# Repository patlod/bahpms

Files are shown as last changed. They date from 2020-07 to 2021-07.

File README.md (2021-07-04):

# bahpms

Thesis Project:  Development and Evaluation of a Hybrid Power Management System for Airships Intended for Infrared Thermographic Inspection of Photovoltaic Plants

## Airship Prototype
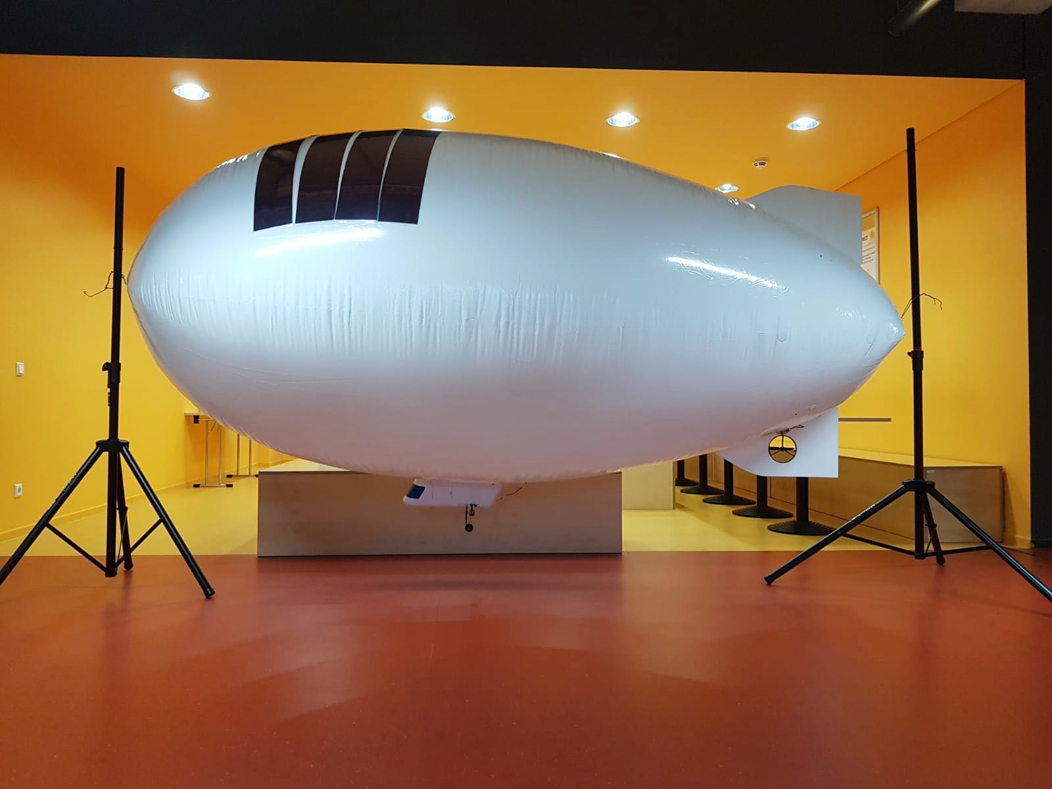
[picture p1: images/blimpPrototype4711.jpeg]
Airship


## Concept
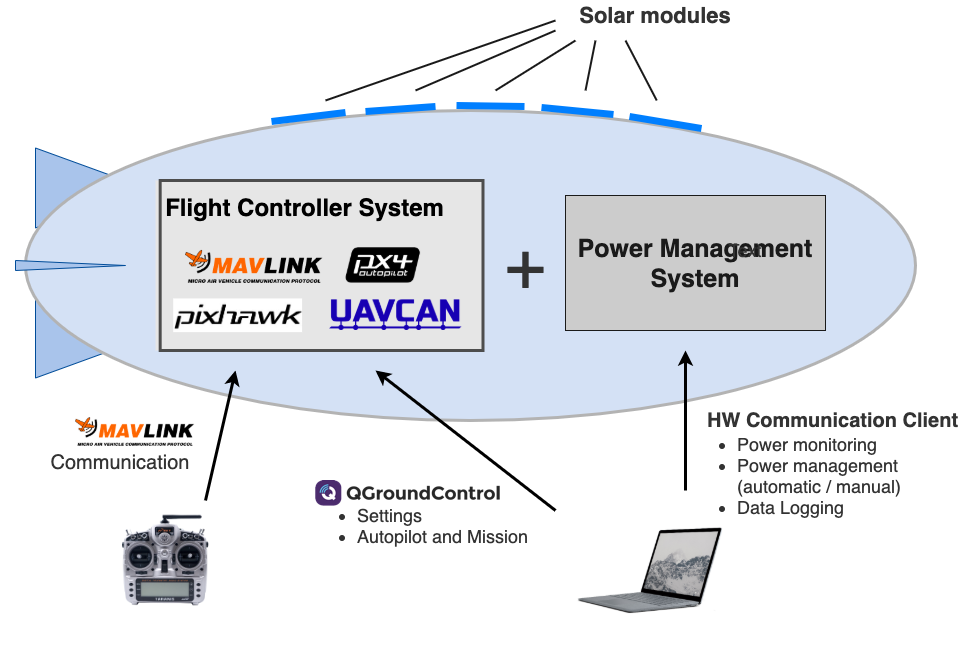
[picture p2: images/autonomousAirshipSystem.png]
Autonomous Airship System


### Inteded Mission
While vehcile monitors photovoltaic plants it will extend its flight time by charging itself with solar power.

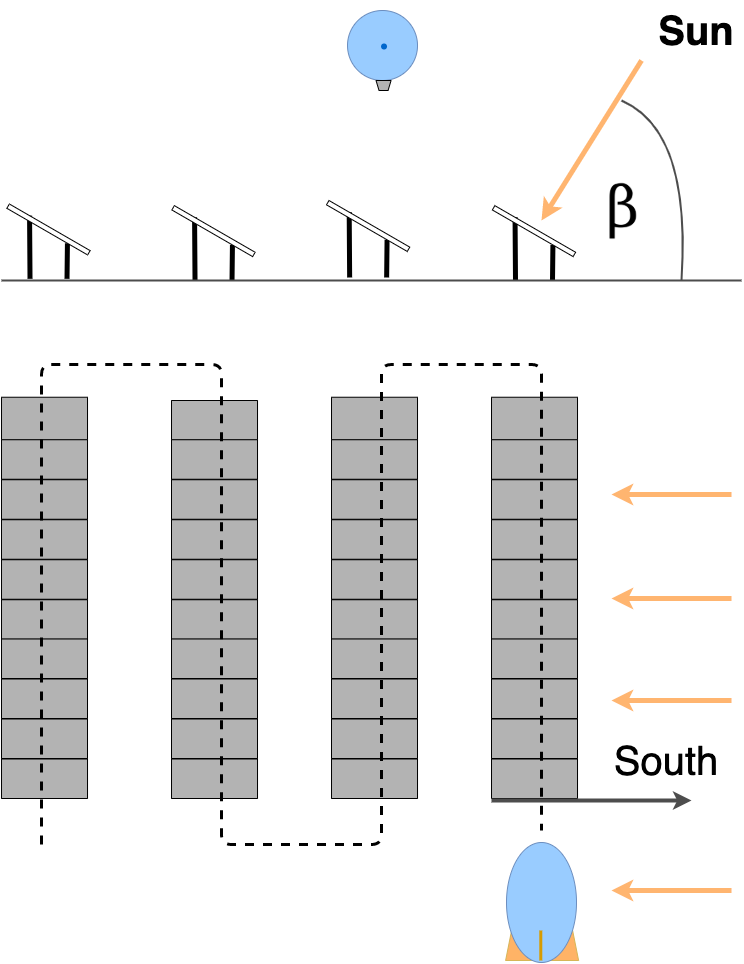
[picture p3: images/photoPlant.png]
PV Plant Monitoring

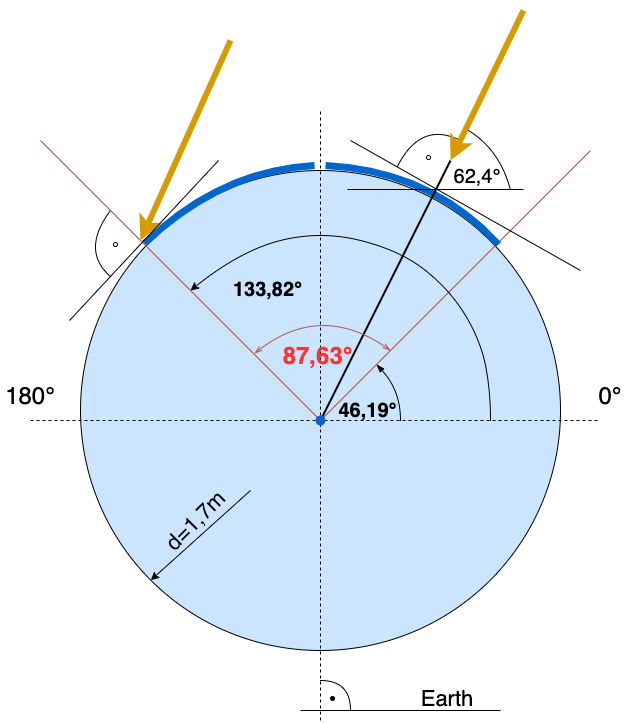
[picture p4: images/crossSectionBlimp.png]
Irradiation Cross Section Blimp


## Gondola & Vehicle Control
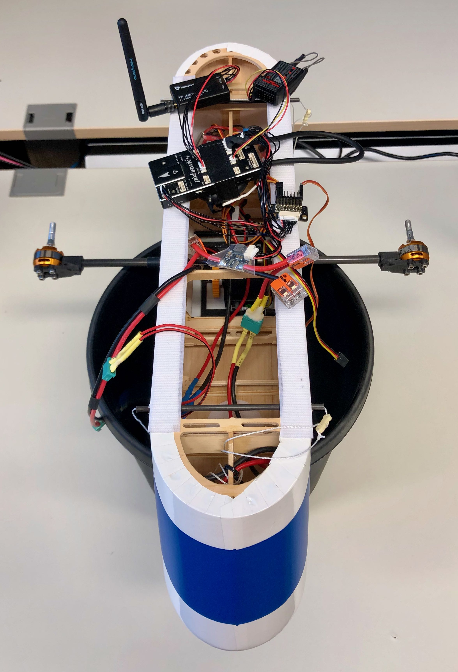
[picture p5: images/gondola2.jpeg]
Gondola


## Hybrid Power Management System (HPMS)
Hardware which manages the charging process of the vehicle and switching between power supplies.

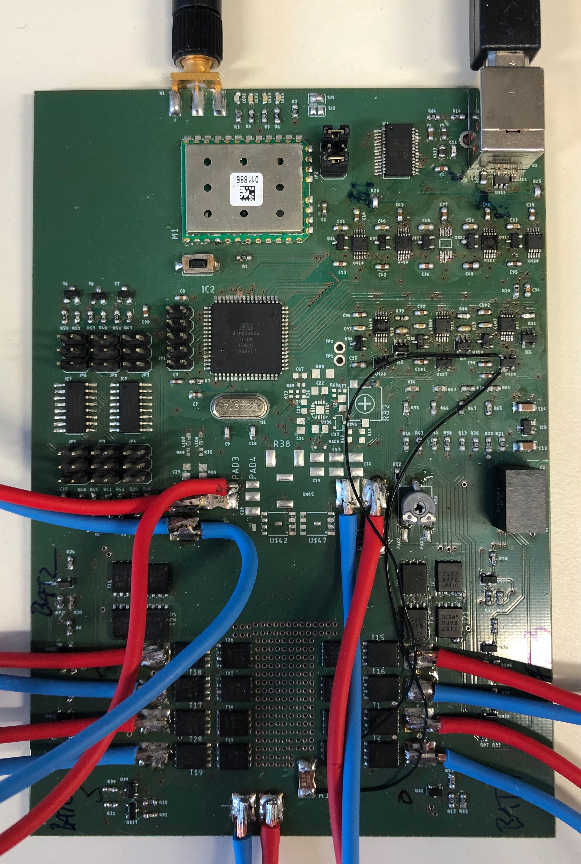
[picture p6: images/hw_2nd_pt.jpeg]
HPMS


## Testing HPMS
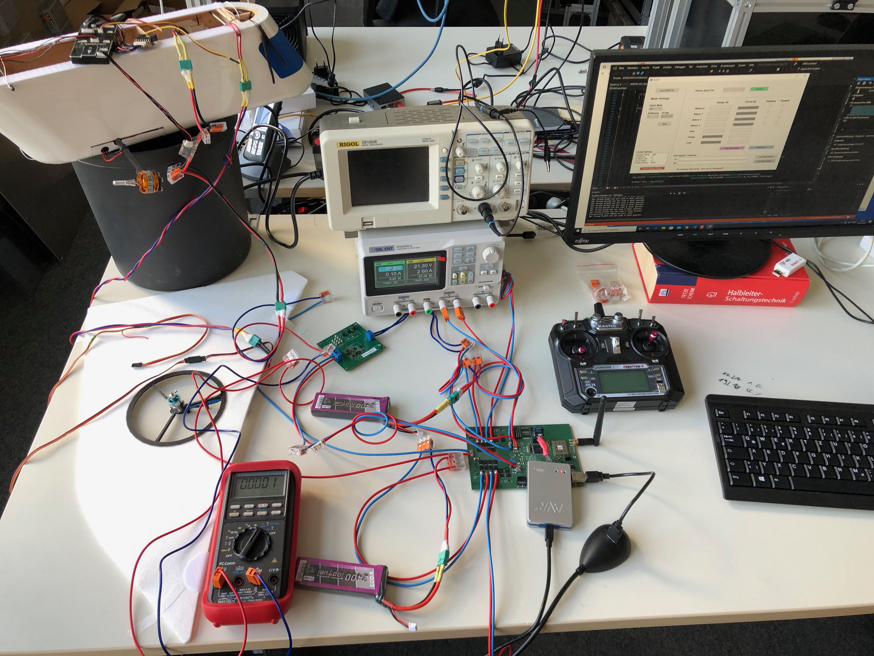
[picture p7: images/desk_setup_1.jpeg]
Testing


## Hardware Communication Client on the Ground
### Concept
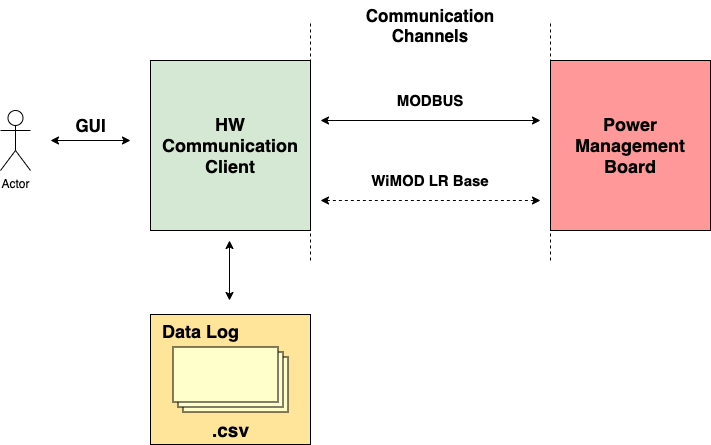
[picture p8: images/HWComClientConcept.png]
Hardware Communication Client Concept


Wireless data exchange with vehicle hardware including charge states, charge rates, battery information (which is currently active and which is charged), manually switch between power supplies, etc.

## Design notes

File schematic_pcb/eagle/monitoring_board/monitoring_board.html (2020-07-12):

Stückliste exportiert aus C:/Users/ar/Desktop/ba/pcb/energy_monitoring/monitoring_board/monitoring_board.sch am 17.03.2020 00:10

Qty | Value | Device | Package | Parts | Description | MF | MPN | OC_FARNELL | OC_NEWARK | POPULARITY | PROD_ID | SF_SKU | SPICEPREFIX | TP_SIGNAL_NAME
6 | | BC847C-NPN-SOT23-BEC | SOT23-BEC | T3, T4, T5, T6, T7, T8 | NPN Transistror
1 | | PINHD-2X3 | 2X03 | JP2 | PIN HEADER | | | | | 62
6 | | PINHD-2X3_2.54 | 2X03 | JP3, JP4, JP5, JP6, JP7, JP8 | PIN HEADER
1 | | PINHD-2X5 | 2X05 | JP1 | PIN HEADER | | | | | 35
1 | | R-TRIMM | RTRIMCA6 | R82 | Trimm resistor
15 | | SI7157DP | SI7157DP | T2, T9, T10, T11, T12, T15, T16, T17, T18, T19, T20, T21, T22, T23, T24 | Vishay Siliconix - Si157DP -- P-Channel 20V (D-S) MOSFET
9 | | SI7157DP | SI7157DP | T1, T13, T14, T25, T26, T27, T28, T29, T30 | Vishay Siliconix - Si157DP -- P-Channel 20V (D-S) MOSFET | | | | | | | | J
2 | | SJ | SJ | SJ1, SJ2 | SMD solder JUMPER | | | | | 33
4 | 0 | R-EU_R0603 | R0603 | R47, R64, R65, R78 | RESISTOR, European symbol
1 | 0.1uF | C-EUC0603K | C0603K | C28 | CAPACITOR, European symbol | | | | | 30 | | | C
1 | 0R | R-EU_R0402 | R0402 | R73 | RESISTOR, European symbol | | | | | 0 | | | R
9 | 0R | R-EU_R0603 | R0603 | R10, R19, R23, R25, R27, R54, R55, R66, R67 | RESISTOR, European symbol
2 | 0R003 | R-EU_R2512 | R2512 | R120, R121 | RESISTOR, European symbol
1 | 0R0065 | R-EU_R2512 | R2512 | R38 | RESISTOR, European symbol
1 | 100k 1% | R-EU_R0402 | R0402 | R37 | RESISTOR, European symbol | | | | | 0 | | | R
24 | 100n | C-EUC0603 | C0603 | C3, C4, C6, C7, C8, C13, C15, C16, C18, C30, C35, C36, C37, C38, C42, C43, C48, C49, C95, C96, C98, C99, C101, C102 | CAPACITOR, European symbol
1 | 100nF | C-EUC0805 | C0805 | C27 | CAPACITOR, European symbol | | | | | 88 | | | C
1 | 10R | R-EU_R1206 | R1206 | R85 | RESISTOR, European symbol | | | | | 41 | | | R
3 | 10k | R-EU_R0402 | R0402 | R68, R69, R75 | RESISTOR, European symbol | | | | | 0 | | | R
11 | 10k | R-EU_R0603 | R0603 | R13, R14, R22, R29, R40, R41, R44, R51, R57, R58, R59 | RESISTOR, European symbol
1 | 10k | R-TRIMM | RTRIMCA6 | R56 | Trimm resistor
1 | 10n | C-EUC0603 | C0603 | C11 | CAPACITOR, European symbol
7 | 10u | C-EUC0603 | C0603 | C21, C23, C40, C46, C52, C97, C100 | CAPACITOR, European symbol
1 | 10u/5,6V | C-EUC1206 | C1206 | C2 | CAPACITOR, European symbol | | | | | 54 | | | C
1 | 10u/5.6V | C-EUC0603 | C0603 | C103 | CAPACITOR, European symbol
1 | 10uF | C-EUC1210 | C1210 | C20 | CAPACITOR, European symbol | | | | | 0 | | | C
2 | 10uF/35V | C-EUC1210 | C1210 | C19, C31 | CAPACITOR, European symbol | | | | | 0 | | | C
2 | 150k 1% | R-EU_R0402 | R0402 | R36, R88 | RESISTOR, European symbol | | | | | 0 | | | R
1 | 15k | R-EU_R0402 | R0402 | R77 | RESISTOR, European symbol | | | | | 0 | | | R
4 | 18k | R-EU_R0603 | R0603 | R9, R15, R17, R39 | RESISTOR, European symbol | | | | | 70 | | | R
1 | 18k | R-EU_R0603 | R0603 | R106 | RESISTOR, European symbol
9 | 1k | R-EU_R0603 | R0603 | R24, R26, R28, R30, R33, R34, R35, R53, R60 | RESISTOR, European symbol | | | | | 70 | | | R
12 | 1k | R-EU_R0603 | R0603 | R8, R11, R31, R32, R42, R45, R46, R48, R49, R52, R63, R91 | RESISTOR, European symbol
1 | 1u/5,6V | C-EUC1206 | C1206 | C12 | CAPACITOR, European symbol | | | | | 54 | | | C
1 | 1u/5.6V | C-EUC1206 | C1206 | C14 | CAPACITOR, European symbol | | | | | 54 | | | C
1 | 1u/6,3V | C-EUC0603 | C0603 | C1 | CAPACITOR, European symbol
3 | 1uF | C-EUC0805 | C0805 | C22, C24, C26 | CAPACITOR, European symbol | | | | | 88 | | | C
1 | 2.2uF | C-EUC0805 | C0805 | C29 | CAPACITOR, European symbol | | | | | 88 | | | C
3 | 22p | C-EUC0603 | C0603 | C9, C10, C87 | CAPACITOR, European symbol
1 | 22u/35V | C-EUC1210 | C1210 | C17 | CAPACITOR, European symbol | | | | | 0 | | | C
1 | 2N7002 | 2N7002 | 2N7002 | U$46 | 2N7002E -- Vishay Siliconix
1 | 2R | R-EU_R2012 | R2012 | R86 | RESISTOR, European symbol | | | | | 0 | | | R
3 | 3300p | C-EUC0603 | C0603 | C32, C33, C34 | CAPACITOR, European symbol
4 | 3k9 | R-EU_R0603 | R0603 | R21, R43, R50, R76 | RESISTOR, European symbol
1 | 4.7u | C-EUC0603 | C0603 | C5 | CAPACITOR, European symbol
1 | 4.7uH /Würth 784 778 047 | IHLP-2525CZ-01 | IHLP-2525CZ-01 | U$45 | Vishay Dale -- IHLP-2525CZ-01 | | | | | | | | B
2 | 4052D | 4052D | SO16 | IC7, IC8 | Dual 4-channel ANALOG MULTIPLEXER
7 | 47k | R-EU_R0603 | R0603 | R1, R2, R3, R4, R5, R6, R7 | RESISTOR, European symbol
1 | 47u/25V | C-EUC1206 | C1206 | C25 | CAPACITOR, European symbol | | | | | 54 | | | C
1 | 4k7 | R-EU_R0603 | R0603 | R84 | RESISTOR, European symbol
1 | 500 | R-EU_R0603 | R0603 | R20 | RESISTOR, European symbol
2 | 500R | R-EU_R0603 | R0603 | R16, R18 | RESISTOR, European symbol
1 | 500u | R-EU_R2512 | R2512 | R122 | RESISTOR, European symbol
1 | 50k | R-EU_R0603 | R0603 | R12 | RESISTOR, European symbol
1 | 560K | R-EU_R0603 | R0603 | R79 | RESISTOR, European symbol
1 | 560k | R-EU_R0603 | R0603 | R80 | RESISTOR, European symbol
1 | 7.3728 MHz | XTAL/S | QS | Q1 | CRYSTAL | | | | | 59
1 | 820k | R-EU_R0603 | R0603 | R81 | RESISTOR, European symbol
1 | BAT54C | BAT54C | BAT54C | U$48 | Diode, Dual Schottky, 30-V, 200-mA, SOT-23, Fairchild, BAT54C
2 | BLM21PG221SN1 | BLM21PG221SN1 | BLM21PG221SN1 | U$12, U$13 | Murata (R) Chip Ferrite Bead -- BLM21xxxxxxSNx-Series
1 | BQ24650 | BQ24650 | BQ24650 | U$36 | Texas Instruments -- bq24650
1 | DLP11SN900HL2 | DLP11SN900HL2 | DLP11SN900HL2 | U$11 | Murata (R) Chip Common Mode Choke Coil DLP11SNxxxxL2x-Series
1 | DUP2201MR6 | DUP2201MR6 | NUP2201MR6 | U$14 | ON Semiconductor (R) -- ESD Protection Diode -- Low Clamping Voltage
1 | FT232RL | FT232RL | SSOP28 | IC1 | Source: http://www.ftdichip.com/Documents/DataSheets/DS_FT232R_v104.pdf | | FT232RL | 1146032 | 91K9918 | 14
1 | IM-X8X | IM-X8X | IM-X8X | M1 | The iM881Ais a compact, low power, bidirectional radio module for the 868MHz frequency bandusing Semtech’s LoRaTMmodulation technology.
3 | INA138 | INA138 | INA138 | U$27, U$28, U$29 | Texas Instruments -- INA1x8 High-Side Measurement Current Shunt Monitor
1 | MCP1703CB | MCP1703CB | SOT23 | IC3 | 250 mA, 16V, Low Quiescent Current LDO Regulator | | | | | 19
8 | MCP33131-05 | MCP33131-05 | MCP33131-05 | U$3, U$7, U$10, U$15, U$16, U$17, U$20, U$21 | Microchip -- MCP33131/21/11-XX -- 1Msps/500kSPS 16/14/12-Bit Single-Ended Input SAR ADC
1 | MEGA64-A | MEGA64-A | TQFP64 | IC2 | MICROCONTROLLER | | ATMEGA64-16AU | 9171355 | 01M6899 | 1
1 | MOMENTARY-SWITCH-SPST-SMD-6.0X3.5MM | MOMENTARY-SWITCH-SPST-SMD-6.0X3.5MM | TACTILE_SWITCH_SMD_6.0X3.5MM | S1 | Momentary Switch (Pushbutton) - SPST | | | | | | SWCH-00815 | COM-08229
8 | NXP_BC847 | NXP_BC847 | NXP_BC847 | U$2, U$34, U$35, U$37, U$38, U$39, U$40, U$41 | NXP -- BC847 -- NPN General Purpose Transistors
1 | NXP_BC857 | NXP_BC857 | NXP_BC857 | U$9 | NXP - BC856; BC857; BC858 -- PNP General Purpose Transistors
3 | OPA340N | OPA340N | SOT23-5 | IC4, IC5, IC6 | Rail-to-Rail Operational Amplifiers | | OPA340NA/3KG4 | 1234805 | 13M5177
1 | PDS1040 | PDS1040 | PDS1040 | U$49 | Diode, Schottky Rectifier, 40-V, 10-A, PDS1040
1 | PN61729-S | PN61729-S | PN61729-S | X2 | BERG USB connector | | | unknown | unknown | 11
2 | PTR1PAD1-13 | PTR1PAD1-13 | P1-13 | TP1, TP2 | TEST PIN | | | | | 2
8 | REF3125-Q1 | REF31XX-Q1 | REF31XX-Q1 | U$4, U$5, U$6, U$8, U$18, U$19, U$22, U$23 | Texas Instruments REF31xx-Q1 15ppm/°C Maximum, 100-mikroA, SOT-23 Series Voltage Reference
2 | SIR404DP | SIR404DP | SIR404DP | U$42, U$47 | Vishay Siliconix SiR404DP -- N-Channel 20V (D-S) MOSFET
1 | SMA-142-0701-801/806 | SMA-142-0701-801/806 | J502-ND-142-0701-801/806 | X1 | SMA 50 Ohm End Launch Jack Receptacle - Round Contact | JOHNSON COMPONENTS | 142-0701-801 | 1608592 | 90F2624 | 5
12 | SMDPAD | SMDPAD | SMDPAD | +V_LOAD, BAT0+, BAT0-, BAT1+, BAT1-, BAT2+, BAT2-, BAT3+, BAT3-, SOLAR+, SOLAR-, V_LOAD- | SMD Solder Pad -- mainly intended for connecting thicker wires for batteries and motors.
1 | TSR-1-XXXX | TSR-1-XXXX | TSR-1-XXXX | U$1 | Non-Isolated DC/DC Converter (POL) by Traco Power - TSR 1-2433
1 | V+R56 | SMD2 | SMD1,27-2,54 | PAD2 | SMD PAD | | | | | 15
1 | V+R82 | SMD2 | SMD1,27-2,54 | PAD3 | SMD PAD | | | | | 15
1 | V-R56 | SMD2 | SMD1,27-2,54 | PAD1 | SMD PAD | | | | | 15
1 | V-R82 | SMD2 | SMD1,27-2,54 | PAD4 | SMD PAD | | | | | 15
3 | green | LEDCHIP-LED0603 | CHIP-LED0603 | LED1, LED3, LED4 | LED
1 | green | LEDCHIP-LED0603 | CHIP-LED0603 | LED2 | LED | | | | | | | | L
2 | green | LEDCHIPLED_0603 | CHIPLED_0603 | LED5, LED6 | LED | | | | | 28

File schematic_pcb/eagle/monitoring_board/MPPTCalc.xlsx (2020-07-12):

L | C | Resonant Frequency (12kHz<f0<17kHz)
4.7e-06 | 2.2e-05 | 15651.64043
Charge Current |  | Sense Resistor RSR | Power Dissipation at Charge Current | Precharge Current
6 |  | 0.006666666667 | 0.24 | 0.6
Sense Resistor Selected |  | Charge Current | Power Dissipation at Charge Current | Precharge Current
0.0065 |  | 6.153846154 | 0.2461538462 | 0.6153846154
R1 | R2 | Battery Voltage (Fully Charged)
10000 | 30000 | 8.4
R3 | R4 | Vmpp Set Voltage
10000 | 1000 | 13.2
R1 | R2 | Battery Voltage (Fully Charged)
530000 | 210000 | 2.932075472

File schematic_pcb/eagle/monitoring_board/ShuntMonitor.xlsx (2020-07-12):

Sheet: Main Battery
Input Current | Shunt | Load | Reference | Output Voltage | Optimized | Voltage Resolution | Current Resolution at 16 Bit
24 | 0.0005 | 820000 | 2.5 | 1.968 | 78.72% | 3.814697266e-05 | 0.0001163017459
 | Power over shunt
 | 0.288

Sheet: PV Current
Input Current | Shunt | Load | Reference | Output Voltage | Optimized | Voltage Resolution | Current Resolution at 16 Bit
6 | 0.003 | 560000 | 2.5 | 2.016 | 80.64% | 3.814697266e-05 | 0.0001135326567
 | Power over shunt
 | 0.108

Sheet: Charge Current
Input Current | Shunt | Load | Reference | Output Voltage | Optimized | Voltage Resolution | Current Resolution at 16 Bit
6 | 0.003 | 560000 | 2.5 | 2.016 | 80.64% | 3.814697266e-05 | 0.0001135326567
 | Power over shunt
 | 0.108

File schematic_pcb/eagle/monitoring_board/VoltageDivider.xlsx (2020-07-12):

R1 | R2 | Uo=x*Uin | Input Voltage | Output | Reference | Voltage Resolution at 16bit
10000 | 3900 | 0.2805755396 | 8.2 | 2.300719424 | 2.5 | 3.814697266e-05
R1_partial | R2_partial
2.2 | 1
1.8 | 15
3300 | 180
 | 3900

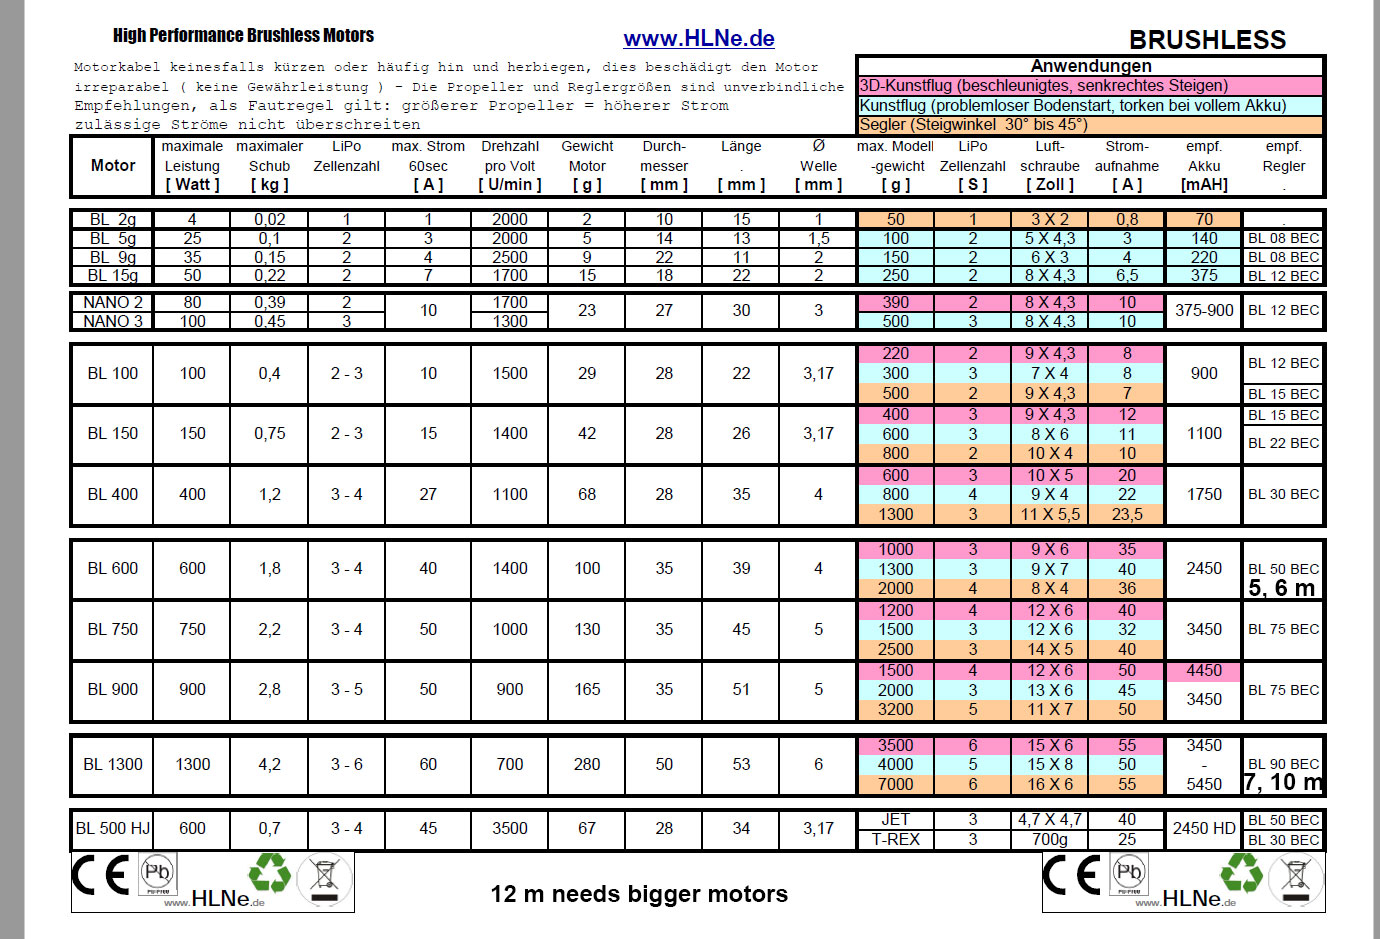
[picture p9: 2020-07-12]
schematic_pcb/datasheets/motors_table_aero_drum.jpg

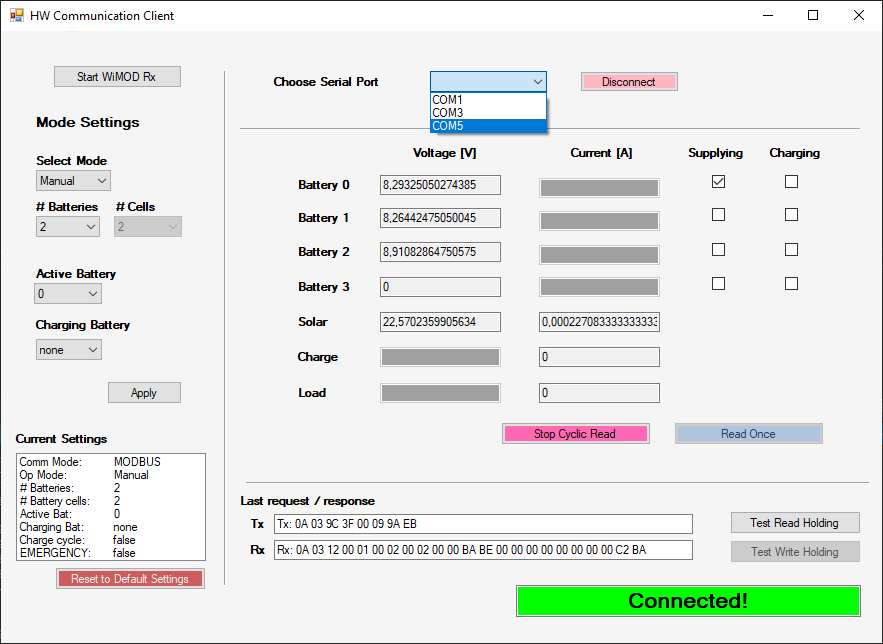
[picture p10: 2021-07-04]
images/screenshot_HWComClient_2.png

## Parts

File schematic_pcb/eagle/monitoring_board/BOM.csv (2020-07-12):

Part | Value | Device | Package | Description | MF | MPN | OC_FARNELL | OC_NEWARK | POPULARITY | PROD_ID | SF_SKU | SPICEPREFIX
C28 | 0.1uF | C-EUC0805 | C0805 | CAPACITOR, European symbol |  |  |  |  | 88 |  |  | C
R23 | 1.8R | R-EU_R0603 | R0603 | RESISTOR, European symbol
R40 | 1.8R | R-EU_R0603 | R0603 | RESISTOR, European symbol
R45 | 1.8R | R-EU_R0603 | R0603 | RESISTOR, European symbol
R52 | 1.8R | R-EU_R0603 | R0603 | RESISTOR, European symbol
C3 | 100n | C-EUC0603 | C0603 | CAPACITOR, European symbol
C4 | 100n | C-EUC0603 | C0603 | CAPACITOR, European symbol
C6 | 100n | C-EUC0603 | C0603 | CAPACITOR, European symbol
C7 | 100n | C-EUC0603 | C0603 | CAPACITOR, European symbol
C8 | 100n | C-EUC0603 | C0603 | CAPACITOR, European symbol
C13 | 100n | C-EUC0603 | C0603 | CAPACITOR, European symbol
C15 | 100n | C-EUC0603 | C0603 | CAPACITOR, European symbol
C16 | 100n | C-EUC0603 | C0603 | CAPACITOR, European symbol
C18 | 100n | C-EUC0603 | C0603 | CAPACITOR, European symbol
C36 | 100n | C-EUC0603 | C0603 | CAPACITOR, European symbol
C37 | 100n | C-EUC0603 | C0603 | CAPACITOR, European symbol
C42 | 100n | C-EUC0603 | C0603 | CAPACITOR, European symbol
C43 | 100n | C-EUC0603 | C0603 | CAPACITOR, European symbol
C48 | 100n | C-EUC0603 | C0603 | CAPACITOR, European symbol
C49 | 100n | C-EUC0603 | C0603 | CAPACITOR, European symbol
C95 | 100n | C-EUC0603 | C0603 | CAPACITOR, European symbol
C96 | 100n | C-EUC0603 | C0603 | CAPACITOR, European symbol
C98 | 100n | C-EUC0603 | C0603 | CAPACITOR, European symbol
C99 | 100n | C-EUC0603 | C0603 | CAPACITOR, European symbol
C101 | 100n | C-EUC0603 | C0603 | CAPACITOR, European symbol
C102 | 100n | C-EUC0603 | C0603 | CAPACITOR, European symbol
C27 | 100nF | C-EUC0805 | C0805 | CAPACITOR, European symbol |  |  |  |  | 88 |  |  | C
R68 | 10k | R-EU_R0402 | R0402 | RESISTOR, European symbol |  |  |  |  | 0 |  |  | R
R69 | 10k | R-EU_R0402 | R0402 | RESISTOR, European symbol |  |  |  |  | 0 |  |  | R
R75 | 10k | R-EU_R0402 | R0402 | RESISTOR, European symbol |  |  |  |  | 0 |  |  | R
C11 | 10n | C-EUC0603 | C0603 | CAPACITOR, European symbol
R85 | 10R | R-EU_R1206 | R1206 | RESISTOR, European symbol |  |  |  |  | 41 |  |  | R
C2 | 10u | C-EUC1206 | C1206 | CAPACITOR, European symbol |  |  |  |  | 54 |  |  | C
C14 | 10u | C-EUC1206 | C1206 | CAPACITOR, European symbol |  |  |  |  | 54 |  |  | C
C21 | 10u | C-EUC0603 | C0603 | CAPACITOR, European symbol
C23 | 10u | C-EUC0603 | C0603 | CAPACITOR, European symbol
C40 | 10u | C-EUC0603 | C0603 | CAPACITOR, European symbol
C46 | 10u | C-EUC0603 | C0603 | CAPACITOR, European symbol
C52 | 10u | C-EUC0603 | C0603 | CAPACITOR, European symbol
C97 | 10u | C-EUC0603 | C0603 | CAPACITOR, European symbol
C100 | 10u | C-EUC0603 | C0603 | CAPACITOR, European symbol
C103 | 10u | C-EUC0603 | C0603 | CAPACITOR, European symbol
C19 | 10uF | C-EUC1210 | C1210 | CAPACITOR, European symbol |  |  |  |  | 0 |  |  | C
C20 | 10uF | C-EUC1210 | C1210 | CAPACITOR, European symbol |  |  |  |  | 0 |  |  | C
R36 | 12k | R-EU_R0402 | R0402 | RESISTOR, European symbol |  |  |  |  | 0 |  |  | R
R77 | 15k | R-EU_R0402 | R0402 | RESISTOR, European symbol |  |  |  |  | 0 |  |  | R
R11 | 15R | R-EU_R0603 | R0603 | RESISTOR, European symbol
R14 | 15R | R-EU_R0603 | R0603 | RESISTOR, European symbol
R41 | 15R | R-EU_R0603 | R0603 | RESISTOR, European symbol
R48 | 15R | R-EU_R0603 | R0603 | RESISTOR, European symbol
R57 | 15R | R-EU_R0603 | R0603 | RESISTOR, European symbol
R70 | 15R | R-EU_R0603 | R0603 | RESISTOR, European symbol
R71 | 15R | R-EU_R0603 | R0603 | RESISTOR, European symbol
R122 | 16m7R | R-EU_R0603 | R0603 | RESISTOR, European symbol
R88 | 180k | R-EU_R0402 | R0402 | RESISTOR, European symbol |  |  |  |  | 0 |  |  | R
R20 | 180R | R-EU_R0603 | R0603 | RESISTOR, European symbol
R42 | 180R | R-EU_R0603 | R0603 | RESISTOR, European symbol
R49 | 180R | R-EU_R0603 | R0603 | RESISTOR, European symbol
R72 | 180R | R-EU_R0603 | R0603 | RESISTOR, European symbol
R9 | 18k | R-EU_R0603 | R0603 | RESISTOR, European symbol |  |  |  |  | 70 |  |  | R
R15 | 18k | R-EU_R0603 | R0603 | RESISTOR, European symbol |  |  |  |  | 70 |  |  | R
R16 | 18k | R-EU_R0603 | R0603 | RESISTOR, European symbol |  |  |  |  | 70 |  |  | R
R17 | 18k | R-EU_R0603 | R0603 | RESISTOR, European symbol |  |  |  |  | 70 |  |  | R
R39 | 18k | R-EU_R0603 | R0603 | RESISTOR, European symbol |  |  |  |  | 70 |  |  | R
R46 | 18k | R-EU_R0603 | R0603 | RESISTOR, European symbol |  |  |  |  | 70 |  |  | R
R61 | 18k | R-EU_R0603 | R0603 | RESISTOR, European symbol
R62 | 18k | R-EU_R0603 | R0603 | RESISTOR, European symbol |  |  |  |  | 70 |  |  | R
R87 | 18k | R-EU_R0402 | R0402 | RESISTOR, European symbol |  |  |  |  | 0 |  |  | R
R106 | 18k | R-EU_R0603 | R0603 | RESISTOR, European symbol
R8 | 1k | R-EU_R0603 | R0603 | RESISTOR, European symbol
R12 | 1k | R-EU_R0603 | R0603 | RESISTOR, European symbol |  |  |  |  | 70 |  |  | R
R24 | 1k | R-EU_R0603 | R0603 | RESISTOR, European symbol |  |  |  |  | 70 |  |  | R
R25 | 1k | R-EU_R0603 | R0603 | RESISTOR, European symbol |  |  |  |  | 70 |  |  | R
R26 | 1k | R-EU_R0603 | R0603 | RESISTOR, European symbol |  |  |  |  | 70 |  |  | R
R27 | 1k | R-EU_R0603 | R0603 | RESISTOR, European symbol |  |  |  |  | 70 |  |  | R
R28 | 1k | R-EU_R0603 | R0603 | RESISTOR, European symbol |  |  |  |  | 70 |  |  | R
R29 | 1k | R-EU_R0603 | R0603 | RESISTOR, European symbol |  |  |  |  | 70 |  |  | R
R30 | 1k | R-EU_R0603 | R0603 | RESISTOR, European symbol |  |  |  |  | 70 |  |  | R
R31 | 1k | R-EU_R0603 | R0603 | RESISTOR, European symbol
R32 | 1k | R-EU_R0603 | R0603 | RESISTOR, European symbol
R33 | 1k | R-EU_R0603 | R0603 | RESISTOR, European symbol |  |  |  |  | 70 |  |  | R
R34 | 1k | R-EU_R0603 | R0603 | RESISTOR, European symbol |  |  |  |  | 70 |  |  | R
R35 | 1k | R-EU_R0603 | R0603 | RESISTOR, European symbol |  |  |  |  | 70 |  |  | R
R53 | 1k | R-EU_R0603 | R0603 | RESISTOR, European symbol |  |  |  |  | 70 |  |  | R
R60 | 1k | R-EU_R0603 | R0603 | RESISTOR, European symbol |  |  |  |  | 70 |  |  | R
R63 | 1k | R-EU_R0603 | R0603 | RESISTOR, European symbol
R10 | 1k8 | R-EU_R0603 | R0603 | RESISTOR, European symbol
R19 | 1k8R | R-EU_R0603 | R0603 | RESISTOR, European symbol
R59 | 1k8R | R-EU_R0603 | R0603 | RESISTOR, European symbol
R18 | 1R | R-EU_R0603 | R0603 | RESISTOR, European symbol
R54 | 1R | R-EU_R0603 | R0603 | RESISTOR, European symbol
R58 | 1R | R-EU_R0603 | R0603 | RESISTOR, European symbol
R64 | 1R | R-EU_R0603 | R0603 | RESISTOR, European symbol
R67 | 1R | R-EU_R0603 | R0603 | RESISTOR, European symbol
R78 | 1R | R-EU_R0603 | R0603 | RESISTOR, European symbol
R83 | 1R | R-EU_R0603 | R0603 | RESISTOR, European symbol
C1 | 1u/6,3V | C-EUC0603 | C0603 | CAPACITOR, European symbol
C22 | 1uF | C-EUC0805 | C0805 | CAPACITOR, European symbol |  |  |  |  | 88 |  |  | C
C24 | 1uF | C-EUC0805 | C0805 | CAPACITOR, European symbol |  |  |  |  | 88 |  |  | C
C26 | 1uF | C-EUC0805 | C0805 | CAPACITOR, European symbol |  |  |  |  | 88 |  |  | C
R13 | 2.2R | R-EU_R0603 | R0603 | RESISTOR, European symbol
R22 | 2.2R | R-EU_R0603 | R0603 | RESISTOR, European symbol
R44 | 2.2R | R-EU_R0603 | R0603 | RESISTOR, European symbol
R51 | 2.2R | R-EU_R0603 | R0603 | RESISTOR, European symbol
C29 | 2.2uF | C-EUC0805 | C0805 | CAPACITOR, European symbol |  |  |  |  | 88 |  |  | C
C17 | 20uF | C-EUC1210 | C1210 | CAPACITOR, European symbol |  |  |  |  | 0 |  |  | C
C9 | 22p | C-EUC0603 | C0603 | CAPACITOR, European symbol
C10 | 22p | C-EUC0603 | C0603 | CAPACITOR, European symbol
C87 | 22p | C-EUC0603 | C0603 | CAPACITOR, European symbol
R73 | 27k | R-EU_R0402 | R0402 | RESISTOR, European symbol |  |  |  |  | 0 |  |  | R
U$46 | 2N7002 | 2N7002 | 2N7002 | 2N7002E -- Vishay Siliconix
R86 | 2R | R-EU_R2012 | R2012 | RESISTOR, European symbol |  |  |  |  | 0 |  |  | R
R37 | 33k | R-EU_R0402 | R0402 | RESISTOR, European symbol |  |  |  |  | 0 |  |  | R
R79 | 39k | R-EU_R0603 | R0603 | RESISTOR, European symbol
R80 | 39kR | R-EU_R0603 | R0603 | RESISTOR, European symbol
R81 | 39kR | R-EU_R0603 | R0603 | RESISTOR, European symbol
R47 | 3k3R | R-EU_R0603 | R0603 | RESISTOR, European symbol
R55 | 3k3R | R-EU_R0603 | R0603 | RESISTOR, European symbol
R65 | 3k3R | R-EU_R0603 | R0603 | RESISTOR, European symbol
R66 | 3k3R | R-EU_R0603 | R0603 | RESISTOR, European symbol
R21 | 3k9R | R-EU_R0603 | R0603 | RESISTOR, European symbol
R43 | 3k9R | R-EU_R0603 | R0603 | RESISTOR, European symbol
R50 | 3k9R | R-EU_R0603 | R0603 | RESISTOR, European symbol
R76 | 3k9R | R-EU_R0603 | R0603 | RESISTOR, European symbol
C5 | 4.7u | C-EUC0603 | C0603 | CAPACITOR, European symbol
U$45 | 4.7uH | IHLP-2525CZ-01 | IHLP-2525CZ-01 | Vishay Dale -- IHLP-2525CZ-01 |  |  |  |  |  |  |  | B
R74 | 470k | R-EU_R0402 | R0402 | RESISTOR, European symbol |  |  |  |  | 0 |  |  | R
R1 | 47k | R-EU_R0603 | R0603 | RESISTOR, European symbol
R2 | 47k | R-EU_R0603 | R0603 | RESISTOR, European symbol
R3 | 47k | R-EU_R0603 | R0603 | RESISTOR, European symbol
R4 | 47k | R-EU_R0603 | R0603 | RESISTOR, European symbol
R5 | 47k | R-EU_R0603 | R0603 | RESISTOR, European symbol
R6 | 47k | R-EU_R0603 | R0603 | RESISTOR, European symbol
R7 | 47k | R-EU_R0603 | R0603 | RESISTOR, European symbol
C12 | 47u | C-EUC1206 | C1206 | CAPACITOR, European symbol |  |  |  |  | 54 |  |  | C
C25 | 47u | C-EUC1206 | C1206 | CAPACITOR, European symbol |  |  |  |  | 54 |  |  | C
Q1 | 7.3728 MHz | XTAL/S | QS | CRYSTAL — TXC DIP HC-49S 9B SERIES |  |  |  |  | 59
R38 | 7.5mR | R-EU_R0603 | R0603 | RESISTOR, European symbol
R120 | 83mR | R-EU_R0603 | R0603 | RESISTOR, European symbol
R121 | 83mR | R-EU_R0603 | R0603 | RESISTOR, European symbol
U$48 | BAT54C | BAT54C | BAT54C | Diode, Dual Schottky, 30-V, 200-mA, SOT-23, Fairchild, BAT54C
U$12 | BLM21PG221SN1 | BLM21PG221SN1 | BLM21PG221SN1 | Murata (R) Chip Ferrite Bead -- BLM21xxxxxxSNx-Series
U$13 | BLM21PG221SN1 | BLM21PG221SN1 | BLM21PG221SN1 | Murata (R) Chip Ferrite Bead -- BLM21xxxxxxSNx-Series
U$15 | BLM21PG221SN1 | BLM21PG221SN1 | BLM21PG221SN1 | Murata (R) Chip Ferrite Bead -- BLM21xxxxxxSNx-Series
U$36 | BQ24650 | BQ24650 | BQ24650 | Texas Instruments -- bq24650
U$11 | DLP11SN900HL2 | DLP11SN900HL2 | DLP11SN900HL2 | Murata (R) Chip Common Mode Choke Coil DLP11SNxxxxL2x-Series
U$14 | DUP2201MR6 | DUP2201MR6 | NUP2201MR6 | ON Semiconductor (R) -- ESD Protection Diode -- Low Clamping Voltage
IC1 | FT232RL | FT232RL | SSOP28 | Source: http://www.ftdichip.com/Documents/DataSheets/DS_FT232R_v104.pdf |  | FT232RL | 1146032 | 91K9918 | 14
LED1 | green | LEDCHIP-LED0603 | CHIP-LED0603 | LED
LED2 | green | LEDCHIP-LED0603 | CHIP-LED0603 | LED |  |  |  |  |  |  |  | L
LED3 | green | LEDCHIP-LED0603 | CHIP-LED0603 | LED
LED4 | green | LEDCHIP-LED0603 | CHIP-LED0603 | LED
LED5 | green | LEDCHIPLED_0603 | CHIPLED_0603 | LED |  |  |  |  | 28
LED6 | green | LEDCHIPLED_0603 | CHIPLED_0603 | LED |  |  |  |  | 28
M1 | IM-X8X | IM-X8X | IM-X8X | The iM881Ais a compact, low power, bidirectional radio module for the 868MHz frequency bandusing Semtech’s LoRaTMmodulation technology.
U$27 | INA138 | INA138 | INA138 | Texas Instruments -- INA1x8 High-Side Measurement Current Shunt Monitor
U$28 | INA138 | INA138 | INA138 | Texas Instruments -- INA1x8 High-Side Measurement Current Shunt Monitor
U$29 | INA138 | INA138 | INA138 | Texas Instruments -- INA1x8 High-Side Measurement Current Shunt Monitor
IC3 | MCP1703CB | MCP1703CB | SOT23 | 250 mA, 16V, Low Quiescent Current LDO Regulator |  |  |  |  | 19
U$10 | MCP33131-05 | MCP33131-05 | MCP33131-05 | Microchip -- MCP33131/21/11-XX -- 1Msps/500kSPS 16/14/12-Bit Single-Ended Input SAR ADC
U$16 | MCP33131-05 | MCP33131-05 | MCP33131-05 | Microchip -- MCP33131/21/11-XX -- 1Msps/500kSPS 16/14/12-Bit Single-Ended Input SAR ADC
U$17 | MCP33131-05 | MCP33131-05 | MCP33131-05 | Microchip -- MCP33131/21/11-XX -- 1Msps/500kSPS 16/14/12-Bit Single-Ended Input SAR ADC
U$20 | MCP33131-05 | MCP33131-05 | MCP33131-05 | Microchip -- MCP33131/21/11-XX -- 1Msps/500kSPS 16/14/12-Bit Single-Ended Input SAR ADC
U$21 | MCP33131-05 | MCP33131-05 | MCP33131-05 | Microchip -- MCP33131/21/11-XX -- 1Msps/500kSPS 16/14/12-Bit Single-Ended Input SAR ADC
U$24 | MCP33131-05 | MCP33131-05 | MCP33131-05 | Microchip -- MCP33131/21/11-XX -- 1Msps/500kSPS 16/14/12-Bit Single-Ended Input SAR ADC
U$25 | MCP33131-05 | MCP33131-05 | MCP33131-05 | Microchip -- MCP33131/21/11-XX -- 1Msps/500kSPS 16/14/12-Bit Single-Ended Input SAR ADC
U$26 | MCP33131-05 | MCP33131-05 | MCP33131-05 | Microchip -- MCP33131/21/11-XX -- 1Msps/500kSPS 16/14/12-Bit Single-Ended Input SAR ADC
IC2 | MEGA64-A | MEGA64-A | TQFP64 | MICROCONTROLLER, AVR ATmega64 |  | ATMEGA64-16AU | 9171355 | 01M6899 | 1
S1 | MOMENTARY-SWITCH-SPST-SMD-6.0X3.5MM | MOMENTARY-SWITCH-SPST-SMD-6.0X3.5MM | TACTILE_SWITCH_SMD_6.0X3.5MM | Momentary Switch (Pushbutton) - SPST |  |  |  |  |  | SWCH-00815 | COM-08229
U$2 | NXP_BC847 | NXP_BC847 | NXP_BC847 | NXP -- BC847 -- NPN General Purpose Transistors
U$34 | NXP_BC847 | NXP_BC847 | NXP_BC847 | NXP -- BC847 -- NPN General Purpose Transistors
U$35 | NXP_BC847 | NXP_BC847 | NXP_BC847 | NXP -- BC847 -- NPN General Purpose Transistors
U$37 | NXP_BC847 | NXP_BC847 | NXP_BC847 | NXP -- BC847 -- NPN General Purpose Transistors
U$38 | NXP_BC847 | NXP_BC847 | NXP_BC847 | NXP -- BC847 -- NPN General Purpose Transistors
U$39 | NXP_BC847 | NXP_BC847 | NXP_BC847 | NXP -- BC847 -- NPN General Purpose Transistors
U$40 | NXP_BC847 | NXP_BC847 | NXP_BC847 | NXP -- BC847 -- NPN General Purpose Transistors
U$41 | NXP_BC847 | NXP_BC847 | NXP_BC847 | NXP -- BC847 -- NPN General Purpose Transistors
U$44 | NXP_BC847 | NXP_BC847 | NXP_BC847 | NXP -- BC847 -- NPN General Purpose Transistors
U$3 | NXP_BC857 | NXP_BC857 | NXP_BC857 | NXP - BC856; BC857; BC858 -- PNP General Purpose Transistors
U$7 | NXP_BC857 | NXP_BC857 | NXP_BC857 | NXP - BC856; BC857; BC858 -- PNP General Purpose Transistors
U$9 | NXP_BC857 | NXP_BC857 | NXP_BC857 | NXP - BC856; BC857; BC858 -- PNP General Purpose Transistors
U$30 | NXP_BC857 | NXP_BC857 | NXP_BC857 | NXP - BC856; BC857; BC858 -- PNP General Purpose Transistors
U$31 | NXP_BC857 | NXP_BC857 | NXP_BC857 | NXP - BC856; BC857; BC858 -- PNP General Purpose Transistors
U$32 | NXP_BC857 | NXP_BC857 | NXP_BC857 | NXP - BC856; BC857; BC858 -- PNP General Purpose Transistors
U$33 | NXP_BC857 | NXP_BC857 | NXP_BC857 | NXP - BC856; BC857; BC858 -- PNP General Purpose Transistors
U$43 | NXP_BC857 | NXP_BC857 | NXP_BC857 | NXP - BC856; BC857; BC858 -- PNP General Purpose Transistors
U$49 | PDS1040 | PDS1040 | PDS1040 | Diode, Schottky Rectifier, 40-V, 10-A, PDS1040
X2 | PN61729-S | PN61729-S | PN61729-S | BERG USB connector |  |  | unknown | unknown | 11
U$4 | REF31XX-Q1 | REF31XX-Q1 | REF31XX-Q1 | Texas Instruments REF31xx-Q1 15ppm/°C Maximum, 100-mikroA, SOT-23 Series Voltage Reference
U$5 | REF31XX-Q1 | REF31XX-Q1 | REF31XX-Q1 | Texas Instruments REF31xx-Q1 15ppm/°C Maximum, 100-mikroA, SOT-23 Series Voltage Reference
U$6 | REF31XX-Q1 | REF31XX-Q1 | REF31XX-Q1 | Texas Instruments REF31xx-Q1 15ppm/°C Maximum, 100-mikroA, SOT-23 Series Voltage Reference
U$8 | REF31XX-Q1 | REF31XX-Q1 | REF31XX-Q1 | Texas Instruments REF31xx-Q1 15ppm/°C Maximum, 100-mikroA, SOT-23 Series Voltage Reference
U$18 | REF31XX-Q1 | REF31XX-Q1 | REF31XX-Q1 | Texas Instruments REF31xx-Q1 15ppm/°C Maximum, 100-mikroA, SOT-23 Series Voltage Reference
U$19 | REF31XX-Q1 | REF31XX-Q1 | REF31XX-Q1 | Texas Instruments REF31xx-Q1 15ppm/°C Maximum, 100-mikroA, SOT-23 Series Voltage Reference
U$22 | REF31XX-Q1 | REF31XX-Q1 | REF31XX-Q1 | Texas Instruments REF31xx-Q1 15ppm/°C Maximum, 100-mikroA, SOT-23 Series Voltage Reference
U$23 | REF31XX-Q1 | REF31XX-Q1 | REF31XX-Q1 | Texas Instruments REF31xx-Q1 15ppm/°C Maximum, 100-mikroA, SOT-23 Series Voltage Reference
U$42 | SIR404DP | SIR404DP | SIR404DP | Vishay Siliconix SiR404DP -- N-Channel 20V (D-S) MOSFET
U$47 | SIR404DP | SIR404DP | SIR404DP | Vishay Siliconix SiR404DP -- N-Channel 20V (D-S) MOSFET
X1 | SMA-142-0701-801/806 | SMA-142-0701-801/806 | J502-ND-142-0701-801/806 | SMA 50 Ohm End Launch Jack Receptacle - Round Contact | JOHNSON COMPONENTS | 142-0701-801 | 1608592 | 90F2624 | 5
+V_LOAD | SMDPAD | SMDPAD | SMDPAD | SMD Solder Pad -- mainly intended for connecting thicker wires for batteries and motors.
BAT0+ | SMDPAD | SMDPAD | SMDPAD | SMD Solder Pad -- mainly intended for connecting thicker wires for batteries and motors.
BAT0- | SMDPAD | SMDPAD | SMDPAD | SMD Solder Pad -- mainly intended for connecting thicker wires for batteries and motors.
BAT1+ | SMDPAD | SMDPAD | SMDPAD | SMD Solder Pad -- mainly intended for connecting thicker wires for batteries and motors.
BAT1- | SMDPAD | SMDPAD | SMDPAD | SMD Solder Pad -- mainly intended for connecting thicker wires for batteries and motors.
BAT2+ | SMDPAD | SMDPAD | SMDPAD | SMD Solder Pad -- mainly intended for connecting thicker wires for batteries and motors.
BAT2- | SMDPAD | SMDPAD | SMDPAD | SMD Solder Pad -- mainly intended for connecting thicker wires for batteries and motors.
BAT3+ | SMDPAD | SMDPAD | SMDPAD | SMD Solder Pad -- mainly intended for connecting thicker wires for batteries and motors.
BAT3- | SMDPAD | SMDPAD | SMDPAD | SMD Solder Pad -- mainly intended for connecting thicker wires for batteries and motors.
SOLAR+ | SMDPAD | SMDPAD | SMDPAD | SMD Solder Pad -- mainly intended for connecting thicker wires for batteries and motors.
SOLAR- | SMDPAD | SMDPAD | SMDPAD | SMD Solder Pad -- mainly intended for connecting thicker wires for batteries and motors.
V_LOAD- | SMDPAD | SMDPAD | SMDPAD | SMD Solder Pad -- mainly intended for connecting thicker wires for batteries and motors.
U$1 | TSR-1-XXXX | TSR-1-XXXX | TSR-1-XXXX | Non-Isolated DC/DC Converter (POL) by Traco Power - TSR 1-2433
PAD1 | V-R56 | SMD2 | SMD1,27-2,54 | SMD PAD |  |  |  |  | 15
PAD4 | V-R82 | SMD2 | SMD1,27-2,54 | SMD PAD |  |  |  |  | 15
PAD2 | V+R56 | SMD2 | SMD1,27-2,54 | SMD PAD |  |  |  |  | 15
PAD3 | V+R82 | SMD2 | SMD1,27-2,54 | SMD PAD |  |  |  |  | 15
JP1 |  | PINHD-2X5 | 2X05 | PIN HEADER |  |  |  |  | 35
JP2 |  | PINHD-2X3 | 2X03 | PIN HEADER |  |  |  |  | 62
R56 |  | R-TRIMM | RTRIMCA6 | Trimm resistor — CA6 Carbon Potentiometers CA
R82 |  | R-TRIMM | RTRIMCA6 | Trimm resistor — CA6 Carbon Potentiometers CA
T1 |  | SI7157DP | SI7157DP | Vishay Siliconix - Si157DP -- P-Channel 20V (D-S) MOSFET |  |  |  |  |  |  |  | J
T2 |  | SI7157DP | SI7157DP | Vishay Siliconix - Si157DP -- P-Channel 20V (D-S) MOSFET
T15 |  | SI7157DP | SI7157DP | Vishay Siliconix - Si157DP -- P-Channel 20V (D-S) MOSFET
T16 |  | SI7157DP | SI7157DP | Vishay Siliconix - Si157DP -- P-Channel 20V (D-S) MOSFET
T17 |  | SI7157DP | SI7157DP | Vishay Siliconix - Si157DP -- P-Channel 20V (D-S) MOSFET
T18 |  | SI7157DP | SI7157DP | Vishay Siliconix - Si157DP -- P-Channel 20V (D-S) MOSFET
T19 |  | SI7157DP | SI7157DP | Vishay Siliconix - Si157DP -- P-Channel 20V (D-S) MOSFET
T20 |  | SI7157DP | SI7157DP | Vishay Siliconix - Si157DP -- P-Channel 20V (D-S) MOSFET
T21 |  | SI7157DP | SI7157DP | Vishay Siliconix - Si157DP -- P-Channel 20V (D-S) MOSFET
T22 |  | SI7157DP | SI7157DP | Vishay Siliconix - Si157DP -- P-Channel 20V (D-S) MOSFET
T23 |  | SI7157DP | SI7157DP | Vishay Siliconix - Si157DP -- P-Channel 20V (D-S) MOSFET
T24 |  | SI7157DP | SI7157DP | Vishay Siliconix - Si157DP -- P-Channel 20V (D-S) MOSFET

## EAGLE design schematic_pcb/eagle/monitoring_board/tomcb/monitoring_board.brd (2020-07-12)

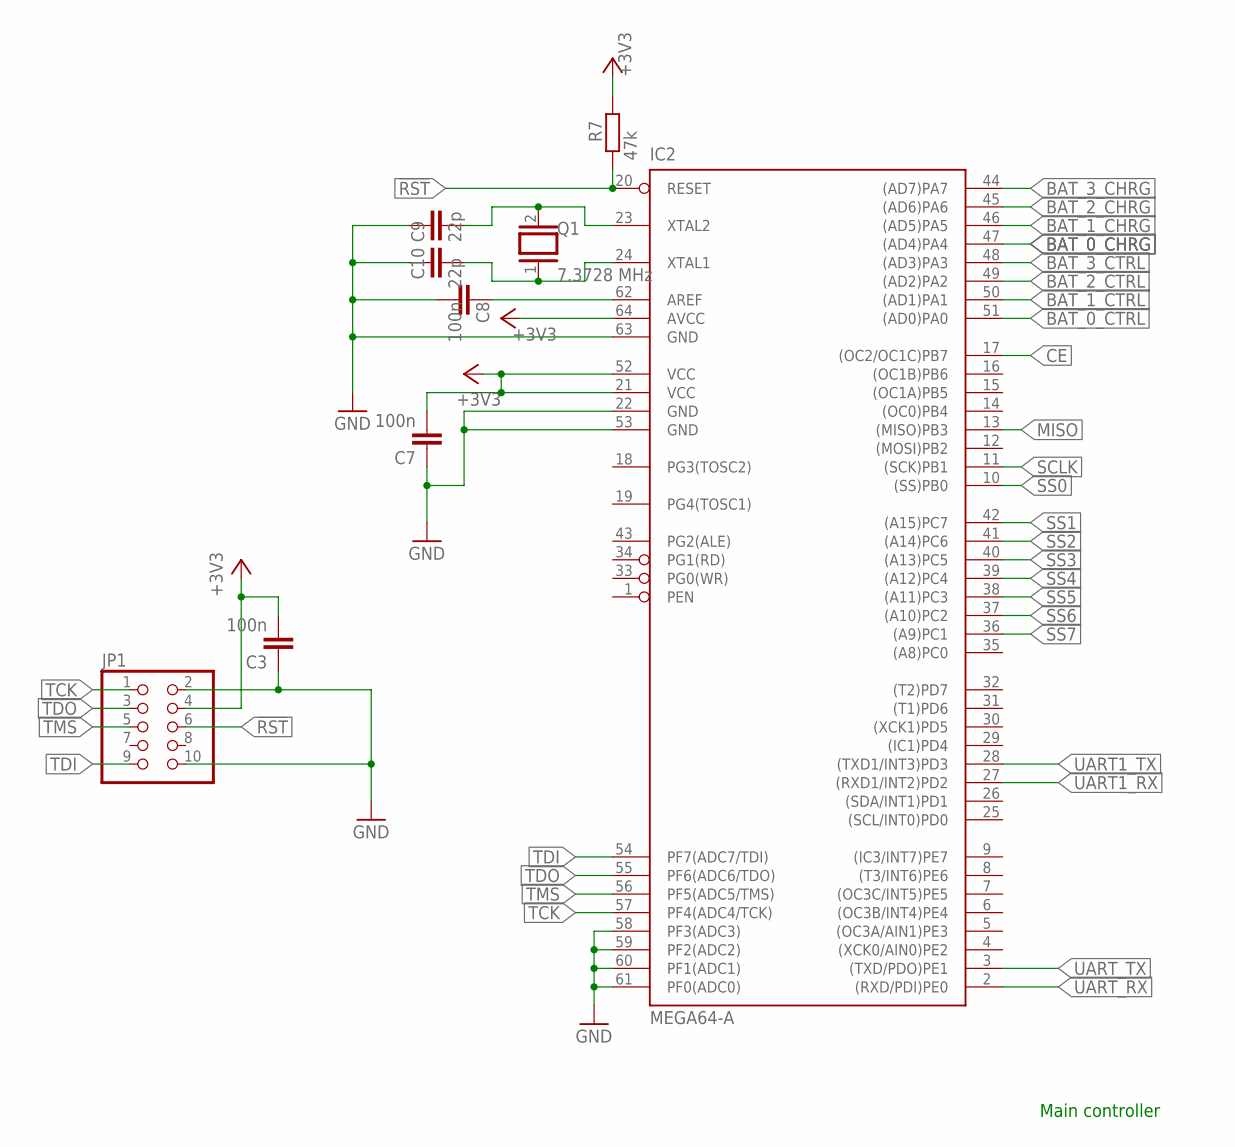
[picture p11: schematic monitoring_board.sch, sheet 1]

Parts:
C3, C7, C8: 100n; C0603
C9, C10: 22p; C0603
IC2: MEGA64-A; TQFP64
JP1: PINHD-2X5; 2X05
Q1: 7.3728 MHz; QS
R7: 47k; R0603

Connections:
!RST: IC2.20 (RESET), JP1.6, R7.1
AREF: C8.1, IC2.62 (AREF)
BAT_0_CHRG: IC2.47 ((AD4)PA4); also elsewhere on the board
BAT_0_CTRL: IC2.51 ((AD0)PA0); also elsewhere on the board
BAT_1_CHRG: IC2.46 ((AD5)PA5); also elsewhere on the board
BAT_1_CTRL: IC2.50 ((AD1)PA1); also elsewhere on the board
BAT_2_CHRG: IC2.45 ((AD6)PA6); also elsewhere on the board
BAT_2_CTRL: IC2.49 ((AD2)PA2); also elsewhere on the board
BAT_3_CHRG: IC2.44 ((AD7)PA7); also elsewhere on the board
BAT_3_CTRL: IC2.48 ((AD3)PA3); also elsewhere on the board
CE: IC2.17 ((OC2/OC1C)PB7); also elsewhere on the board
GND: C3.1, C7.1, C8.2, C9.1, C10.1, IC2.22 (GND), IC2.53 (GND), IC2.58 (PF3(ADC3)), IC2.59 (PF2(ADC2)), IC2.60 (PF1(ADC1)), IC2.61 (PF0(ADC0)), IC2.63 (GND), JP1.2, JP1.10; also elsewhere on the board
MISO: IC2.13 ((MISO)PB3); also elsewhere on the board
unnamed: C9.2, IC2.23 (XTAL2), Q1.2
unnamed: C10.2, IC2.24 (XTAL1), Q1.1
SCLK: IC2.11 ((SCK)PB1); also elsewhere on the board
SS0: IC2.10 ((SS)PB0); also elsewhere on the board
SS1: IC2.42 ((A15)PC7); also elsewhere on the board
SS2: IC2.41 ((A14)PC6); also elsewhere on the board
SS3: IC2.40 ((A13)PC5); also elsewhere on the board
SS4: IC2.39 ((A12)PC4); also elsewhere on the board
SS5: IC2.38 ((A11)PC3); also elsewhere on the board
SS6: IC2.37 ((A10)PC2); also elsewhere on the board
SS7: IC2.36 ((A9)PC1); also elsewhere on the board
TCK: IC2.57 (PF4(ADC4/TCK)), JP1.1
TDI: IC2.54 (PF7(ADC7/TDI)), JP1.9
TDO: IC2.55 (PF6(ADC6/TDO)), JP1.3
TMS: IC2.56 (PF5(ADC5/TMS)), JP1.5
UART1_RX: IC2.27 ((RXD1/INT2)PD2); also elsewhere on the board
UART1_TX: IC2.28 ((TXD1/INT3)PD3); also elsewhere on the board
UART_RX: IC2.2 ((RXD/PDI)PE0); also elsewhere on the board
UART_TX: IC2.3 ((TXD/PDO)PE1); also elsewhere on the board
VCC3V3: C3.2, C7.2, IC2.21 (VCC), IC2.52 (VCC), IC2.64 (AVCC), JP1.4, R7.2; also elsewhere on the board

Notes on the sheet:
Main controller

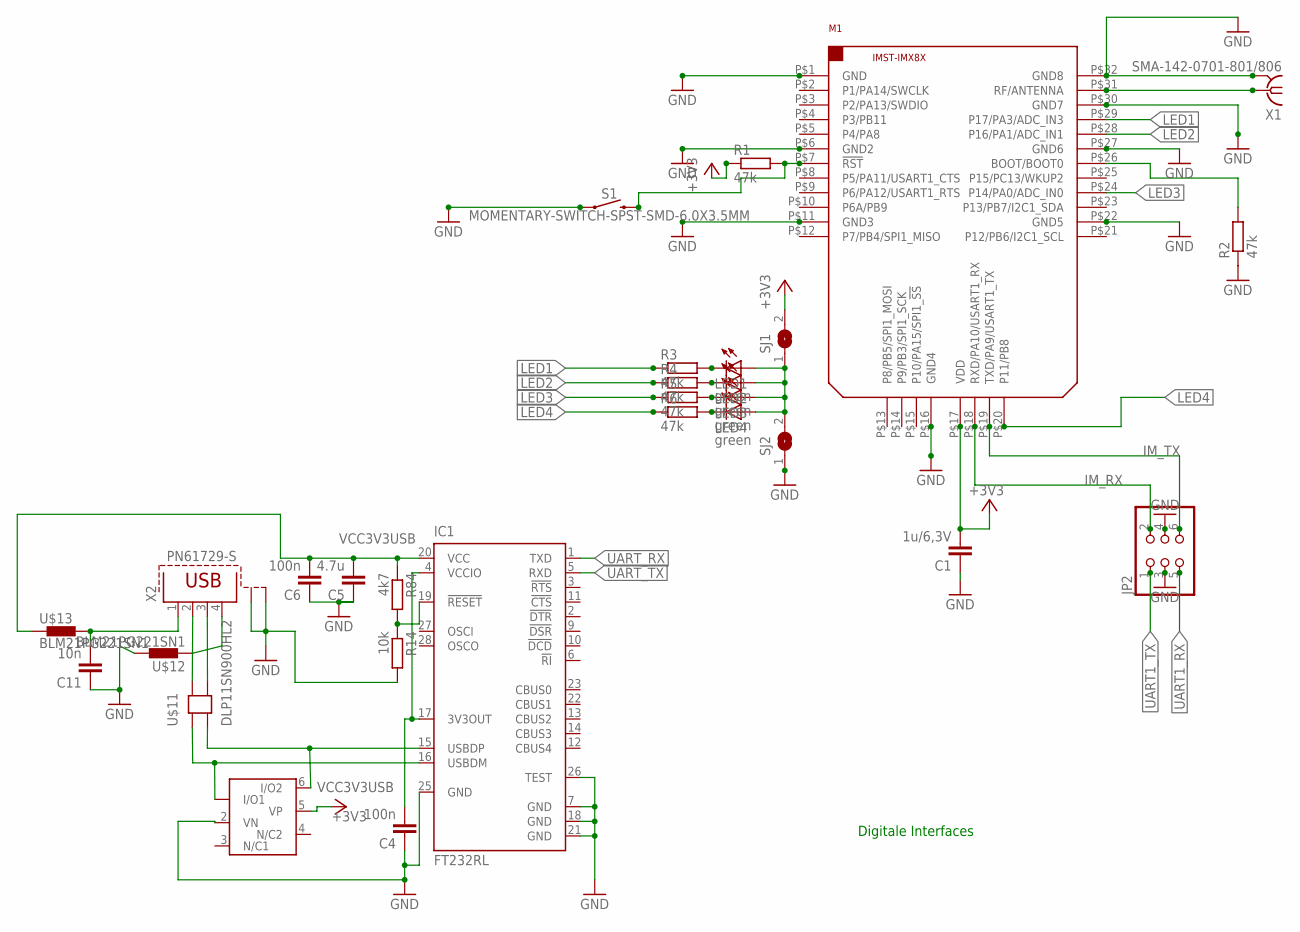
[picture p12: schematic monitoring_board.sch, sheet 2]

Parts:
C1: 1u/6,3V; C0603
C4, C6: 100n; C0603
C5: 4.7u; C0603
C11: 10n; C0603
IC1: FT232RL; SSOP28
JP2: PINHD-2X3; 2X03
LED1, LED2, LED3, LED4: green; CHIP-LED0603
M1: IM-X8X
R1, R2, R3, R4, R5, R6: 47k; R0603
R14: 10k; R0603
R84: 4k7; R0603
S1: MOMENTARY-SWITCH-SPST-SMD-6.0X3.5MM; TACTILE_SWITCH_SMD_6.0X3.5MM
SJ1, SJ2: SJ
U$11: DLP11SN900HL2
U$12, U$13: BLM21PG221SN1
U$14: DUP2201MR6; NUP2201MR6
X1: SMA-142-0701-801/806; J502-ND-142-0701-801/806
X2: PN61729-S

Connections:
3V3OUT: C4.2, IC1.4 (VCCIO), IC1.17 (3V3OUT)
GND: C1.1, C4.1, C5.1, C6.1, C11.1, IC1.7 (GND), IC1.18 (GND), IC1.21 (GND), IC1.25 (GND), IC1.26 (TEST), JP2.3, JP2.4, M1.P$1 (GND), M1.P$6 (GND2), M1.P$11 (GND3), M1.P$16 (GND4), M1.P$22 (GND5), M1.P$27 (GND6), M1.P$30 (GND7), M1.P$32 (GND8), R2.1, R14.2, S1.1, SJ2.1, U$12.2, U$14.2 (VN), X1.G@1 (2), X1.G@2 (2), X1.G@3 (2), X1.G@4 (2), X2.S1, X2.S2; also elsewhere on the board
IM_RX: JP2.2, M1.P$18 (RXD/PA10/USART1_RX)
IM_TX: JP2.6, M1.P$19 (TXD/PA9/USART1_TX)
LED1: M1.P$29 (P17/PA3/ADC_IN3), R3.1
LED2: M1.P$28 (P16/PA1/ADC_IN1), R4.1
LED3: M1.P$24 (P14/PA0/ADC_IN0), R5.1
LED4: M1.P$20 (P11/PB8), R6.1
unnamed: M1.P$31 (RF/ANTENNA), X1.1
unnamed: LED1.C, R3.2
unnamed: M1.P$7 (!RST), R1.2, S1.2
unnamed: M1.P$26 (BOOT/BOOT0), R2.2
unnamed: LED2.C, R4.2
unnamed: LED3.C, R5.2
unnamed: LED4.C, R6.2
unnamed: IC1.19 (!RESET), R14.1, R84.2
unnamed: LED1.A, LED2.A, LED3.A, LED4.A, SJ1.1, SJ2.2
unnamed: U$11.2, X2.2
unnamed: U$11.4, X2.3
unnamed: IC1.16 (USBDM), U$11.1, U$14.1 (I/O1)
unnamed: IC1.15 (USBDP), U$11.3, U$14.6 (I/O2)
unnamed: U$12.1, X2.4
unnamed: C11.2, U$13.2, X2.1
UART1_RX: JP2.5; also elsewhere on the board
UART1_TX: JP2.1; also elsewhere on the board
UART_RX: IC1.1 (TXD); also elsewhere on the board
UART_TX: IC1.5 (RXD); also elsewhere on the board
VCC3V3: C1.2, M1.P$17 (VDD), R1.1, SJ1.2; also elsewhere on the board
VCC3V3USB: C5.2, C6.2, IC1.20 (VCC), R84.1, U$13.1, U$14.5 (VP)

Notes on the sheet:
Digitale Interfaces

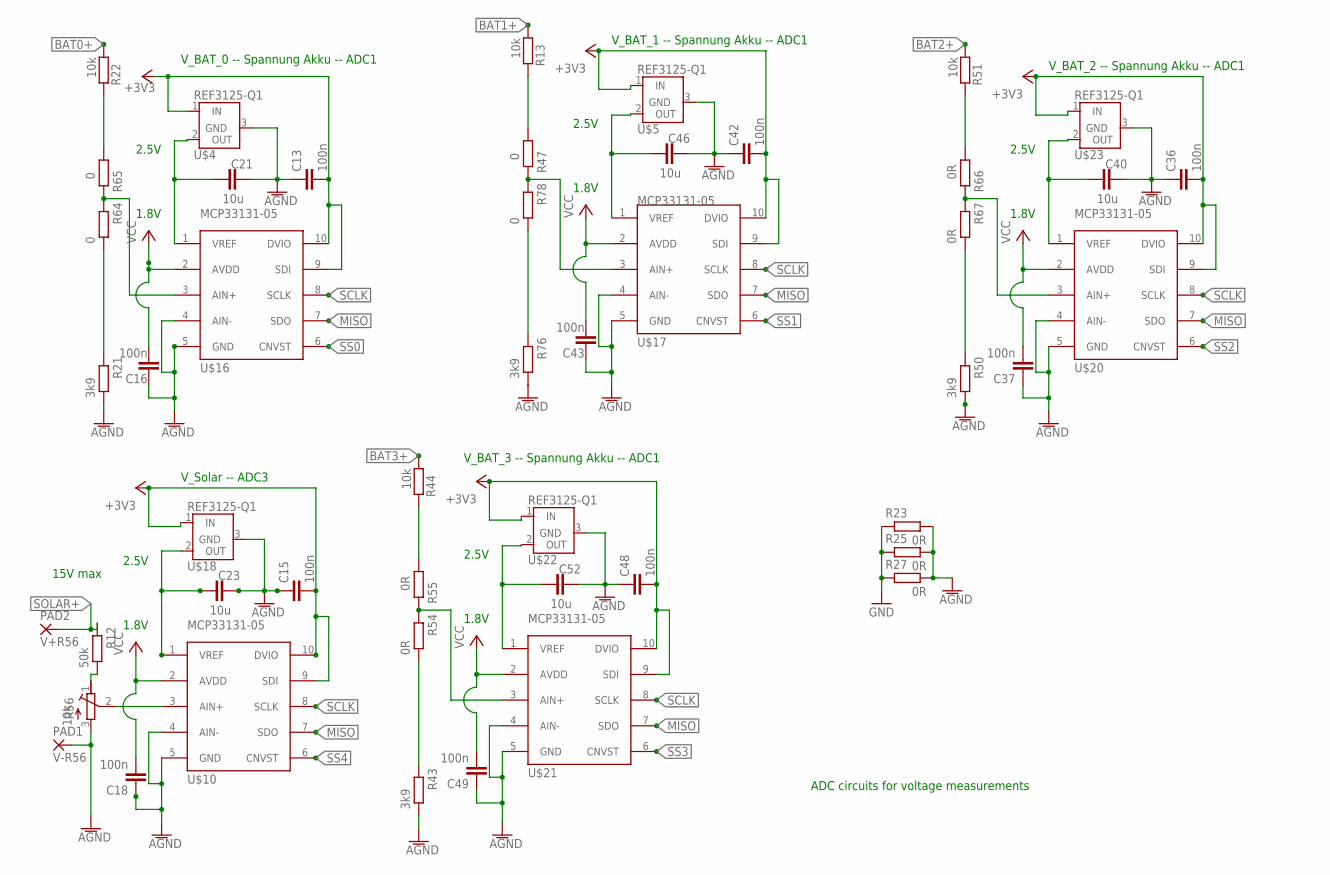
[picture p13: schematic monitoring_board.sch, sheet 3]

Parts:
C13, C15, C16, C18, C36, C37, C42, C43, C48, C49: 100n; C0603
C21, C23, C40, C46, C52: 10u; C0603
PAD1: V-R56; SMD1,27-2,54
PAD2: V+R56; SMD1,27-2,54
R12: 50k; R0603
R13, R22, R44, R51: 10k; R0603
R21, R43, R50, R76: 3k9; R0603
R23, R25, R27, R54, R55, R66, R67: 0R; R0603
R47, R64, R65, R78: 0; R0603
R56: 10k; RTRIMCA6
U$4, U$5, U$18, U$22, U$23: REF3125-Q1; REF31XX-Q1
U$10, U$16, U$17, U$20, U$21: MCP33131-05

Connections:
AGND: C13.1, C15.1, C16.1, C18.1, C21.2, C23.2, C36.1, C37.1, C40.2, C42.1, C43.1, C46.2, C48.1, C49.1, C52.2, PAD1.1, R21.2, R23.2, R25.2, R27.2, R43.2, R50.2, R56.3 (A), R76.2, U$4.3 (GND), U$5.3 (GND), U$10.4 (AIN-), U$10.5 (GND), U$16.4 (AIN-), U$16.5 (GND), U$17.4 (AIN-), U$17.5 (GND), U$18.3 (GND), U$20.4 (AIN-), U$20.5 (GND), U$21.4 (AIN-), U$21.5 (GND), U$22.3 (GND), U$23.3 (GND); also elsewhere on the board
BAT0+: R22.1; also elsewhere on the board
BAT1+: R13.1; also elsewhere on the board
BAT2+: R51.1; also elsewhere on the board
BAT3+: R44.1; also elsewhere on the board
GND: R23.1, R25.1, R27.1; also elsewhere on the board
MISO: U$10.7 (SDO), U$16.7 (SDO), U$17.7 (SDO), U$20.7 (SDO), U$21.7 (SDO); also elsewhere on the board
unnamed: R12.2, R56.1 (E)
unnamed: R51.2, R66.2
unnamed: C23.1, U$10.1 (VREF), U$18.2 (OUT)
unnamed: C21.1, U$4.2 (OUT), U$16.1 (VREF)
unnamed: R56.2 (S), U$10.3 (AIN+)
unnamed: R22.2, R65.2
unnamed: R21.1, R64.2
unnamed: R13.2, R47.2
unnamed: R76.1, R78.2
unnamed: R50.1, R67.2
unnamed: R44.2, R55.2
unnamed: R43.1, R54.2
unnamed: C40.1, U$20.1 (VREF), U$23.2 (OUT)
unnamed: R64.1, R65.1, U$16.3 (AIN+)
unnamed: R66.1, R67.1, U$20.3 (AIN+)
unnamed: C46.1, U$5.2 (OUT), U$17.1 (VREF)
unnamed: R47.1, R78.1, U$17.3 (AIN+)
unnamed: R54.1, R55.1, U$21.3 (AIN+)
unnamed: C52.1, U$21.1 (VREF), U$22.2 (OUT)
SCLK: U$10.8 (SCLK), U$16.8 (SCLK), U$17.8 (SCLK), U$20.8 (SCLK), U$21.8 (SCLK); also elsewhere on the board
SOLAR+: PAD2.1, R12.1; also elsewhere on the board
SS0: U$16.6 (CNVST); also elsewhere on the board
SS1: U$17.6 (CNVST); also elsewhere on the board
SS2: U$20.6 (CNVST); also elsewhere on the board
SS3: U$21.6 (CNVST); also elsewhere on the board
SS4: U$10.6 (CNVST); also elsewhere on the board
VCC1V8: C16.2, C18.2, C37.2, C43.2, C49.2, U$10.2 (AVDD), U$16.2 (AVDD), U$17.2 (AVDD), U$20.2 (AVDD), U$21.2 (AVDD); also elsewhere on the board
VCC3V3: C13.2, C15.2, C36.2, C42.2, C48.2, U$4.1 (IN), U$5.1 (IN), U$10.9 (SDI), U$10.10 (DVIO), U$16.9 (SDI), U$16.10 (DVIO), U$17.9 (SDI), U$17.10 (DVIO), U$18.1 (IN), U$20.9 (SDI), U$20.10 (DVIO), U$21.9 (SDI), U$21.10 (DVIO), U$22.1 (IN), U$23.1 (IN); also elsewhere on the board

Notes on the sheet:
1.8V
2.5V
V_BAT_0 -- Spannung Akku -- ADC1
ADC circuits for voltage measurements
V_BAT_2 -- Spannung Akku -- ADC1
V_BAT_1 -- Spannung Akku -- ADC1
V_BAT_3 -- Spannung Akku -- ADC1
V_Solar -- ADC3
15V max

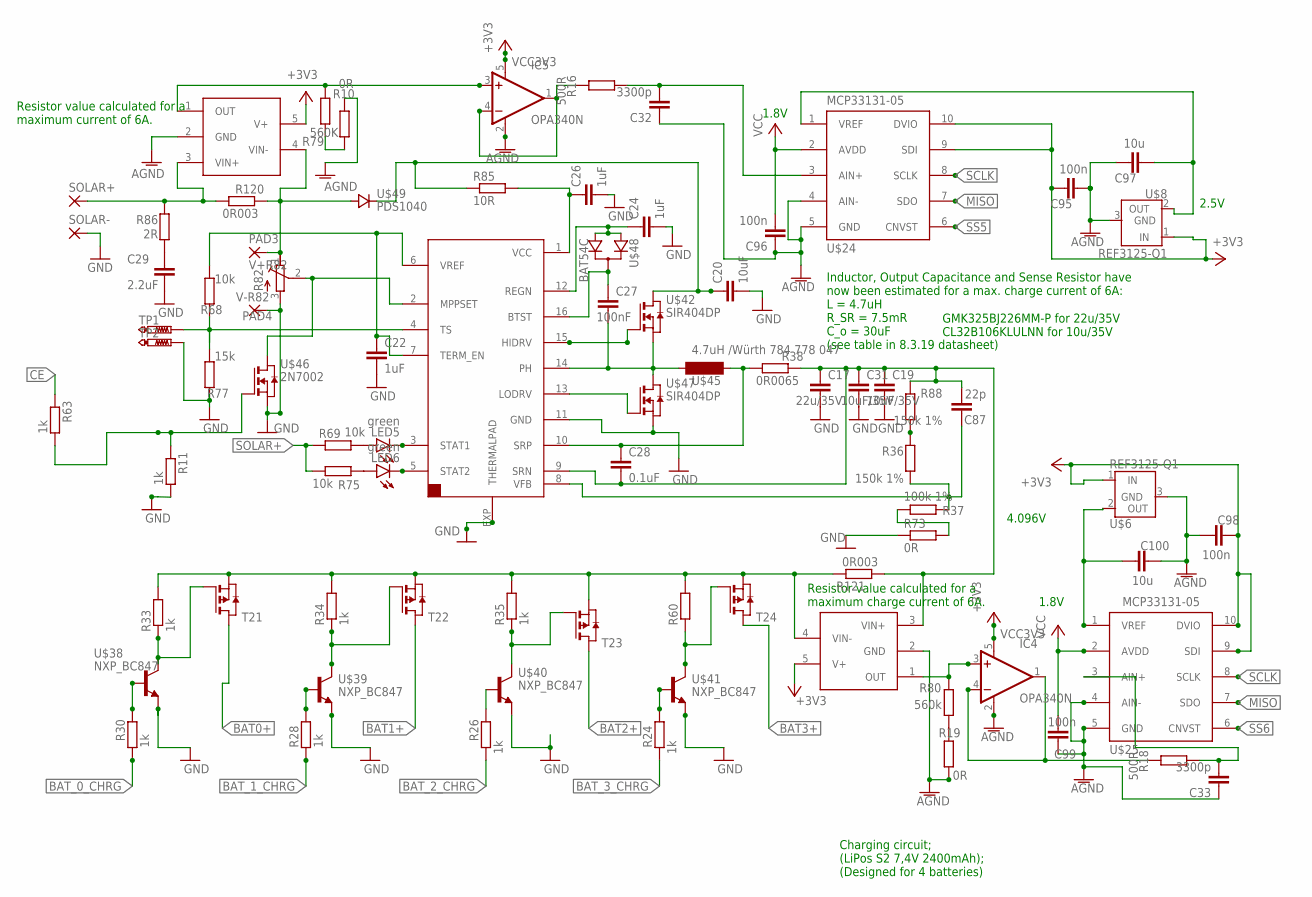
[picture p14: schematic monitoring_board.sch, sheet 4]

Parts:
C17: 22u/35V; C1210
C19, C31: 10uF/35V; C1210
C20: 10uF; C1210
C22, C24, C26: 1uF; C0805
C27: 100nF; C0805
C28: 0.1uF; C0603K
C29: 2.2uF; C0805
C32, C33: 3300p; C0603
C87: 22p; C0603
C95, C96, C98, C99: 100n; C0603
C97, C100: 10u; C0603
IC4, IC5: OPA340N; SOT23-5
LED5, LED6: green; CHIPLED_0603
PAD3: V+R82; SMD1,27-2,54
PAD4: V-R82; SMD1,27-2,54
R10, R19: 0R; R0603
R11, R24, R26, R28, R30, R33, R34, R35, R60, R63: 1k; R0603
R16, R18: 500R; R0603
R36, R88: 150k 1%; R0402
R37: 100k 1%; R0402
R38: 0R0065; R2512
R68, R69, R75: 10k; R0402
R73: 0R; R0402
R77: 15k; R0402
R79: 560K; R0603
R80: 560k; R0603
R82: R-TRIMM; RTRIMCA6
R85: 10R; R1206
R86: 2R; R2012
R120, R121: 0R003; R2512
SOLAR+: SMDPAD
SOLAR-: SMDPAD
T21, T22, T23, T24: SI7157DP
TP1, TP2: PTR1PAD1-13; P1-13
U$6, U$8: REF3125-Q1; REF31XX-Q1
U$24, U$25: MCP33131-05
U$27, U$28: INA138
U$36: BQ24650
U$38, U$39, U$40, U$41: NXP_BC847
U$42, U$47: SIR404DP
U$45: 4.7uH /Würth 784 778 047; IHLP-2525CZ-01
U$46: 2N7002
U$48: BAT54C
U$49: PDS1040

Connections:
AGND: C32.1, C33.1, C95.1, C96.1, C97.2, C98.1, C99.1, C100.2, IC4.2 (V-), IC5.2 (V-), R10.1, R19.1, U$6.3 (GND), U$8.3 (GND), U$24.4 (AIN-), U$24.5 (GND), U$25.4 (AIN-), U$25.5 (GND), U$27.2 (GND), U$28.2 (GND); also elsewhere on the board
AIN+: IC4.3 (+IN), R80.2, U$27.1 (OUT)
BAT0+: T21.5 (D), T21.6 (D), T21.7 (D), T21.8 (D), T21.9 (D); also elsewhere on the board
BAT1+: T22.5 (D), T22.6 (D), T22.7 (D), T22.8 (D), T22.9 (D); also elsewhere on the board
BAT2+: T23.5 (D), T23.6 (D), T23.7 (D), T23.8 (D), T23.9 (D); also elsewhere on the board
BAT3+: T24.5 (D), T24.6 (D), T24.7 (D), T24.8 (D), T24.9 (D); also elsewhere on the board
BAT_0_CHRG: R30.1; also elsewhere on the board
BAT_1_CHRG: R28.1; also elsewhere on the board
BAT_2_CHRG: R26.1; also elsewhere on the board
BAT_3_CHRG: R24.1; also elsewhere on the board
BTST: C27.1, U$36.16 (BTST), U$48.3 (C)
CE: R63.2; also elsewhere on the board
GND: C17.2, C19.2, C20.2, C22.2, C24.2, C26.2, C29.2, C31.2, PAD4.1, R11.1, R73.1, R77.1, R82.3 (A), SOLAR-.1, TP2.TP, U$36.11 (GND), U$36.EXP (THERMALPAD), U$38.2 (E), U$39.2 (E), U$40.2 (E), U$41.2 (E), U$46.2 (S), U$47.1 (S), U$47.2 (S), U$47.3 (S); also elsewhere on the board
HIDRV: U$36.15 (HIDRV), U$42.4 (G)
LODRV: U$36.13 (LODRV), U$47.4 (G)
MISO: U$24.7 (SDO), U$25.7 (SDO); also elsewhere on the board
MPPSET: R82.2 (S), U$36.2 (MPPSET), U$46.3 (D)
unnamed: IC4.1 (OUT), IC4.4 (-IN), R18.1
unnamed: IC5.1 (OUT), IC5.4 (-IN), R16.1
unnamed: R33.1, T21.4 (G), U$38.3 (C)
unnamed: C32.2, R16.2, U$24.3 (AIN+)
unnamed: C33.2, R18.2, U$25.3 (AIN+)
unnamed: IC5.3 (+IN), R79.2, U$28.1 (OUT)
unnamed: R34.1, T22.4 (G), U$39.3 (C)
unnamed: LED5.A, R69.2
unnamed: R35.1, T23.4 (G), U$40.3 (C)
unnamed: LED6.A, R75.2
unnamed: C29.1, R86.1
unnamed: R10.2, R79.1
unnamed: R60.1, T24.4 (G), U$41.3 (C)
unnamed: R26.2, U$40.1 (B)
unnamed: R28.2, U$39.1 (B)
unnamed: R30.2, U$38.1 (B)
unnamed: R24.2, U$41.1 (B)
unnamed: R11.2, R63.1, U$46.1 (G)
unnamed: R36.2, R88.1
unnamed: R19.2, R80.1
unnamed: C87.1, R36.1, R37.2, U$36.8 (VFB)
unnamed: R37.1, R73.2
unnamed: C26.1, R85.2, U$36.1 (VCC)
unnamed: C20.1, R85.1, U$42.5 (D), U$42.6 (D), U$42.7 (D), U$42.8 (D), U$42.9 (D), U$49.P$1 (C)
unnamed: PAD3.1, R82.1 (E), R120.2, U$28.4 (VIN-), U$49.1 (A), U$49.2 (A)
unnamed: C100.1, U$6.2 (OUT), U$25.1 (VREF)
unnamed: R33.2, R34.2, R35.2, R60.2, R121.2, T21.1 (S), T21.2 (S), T21.3 (S), T22.1 (S), T22.2 (S), T22.3 (S), T23.1 (S), T23.2 (S), T23.3 (S), T24.1 (S), T24.2 (S), T24.3 (S), U$27.4 (VIN-)
unnamed: C97.1, U$8.2 (OUT), U$24.1 (VREF)
PH: C27.2, U$36.14 (PH), U$42.1 (S), U$42.2 (S), U$42.3 (S), U$45.1, U$47.5 (D), U$47.6 (D), U$47.7 (D), U$47.8 (D), U$47.9 (D)
REGN: C24.1, U$36.12 (REGN), U$48.1 (A1), U$48.2 (A2)
SCLK: U$24.8 (SCLK), U$25.8 (SCLK); also elsewhere on the board
SOLAR+: R69.1, R75.1, R86.2, R120.1, SOLAR+.1, U$28.3 (VIN+); also elsewhere on the board
SRN: C17.1, C19.1, C28.2, C31.1, C87.2, R38.2, R88.2, R121.1, U$27.3 (VIN+), U$36.9 (SRN)
SRP: C28.1, R38.1, U$36.10 (SRP), U$45.2
SS5: U$24.6 (CNVST); also elsewhere on the board
SS6: U$25.6 (CNVST); also elsewhere on the board
STAT1: LED5.C, U$36.3 (STAT1)
STAT2: LED6.C, U$36.5 (STAT2)
TS: R68.1, R77.2, TP1.TP, U$36.4 (TS)
VCC1V8: C96.2, C99.2, U$24.2 (AVDD), U$25.2 (AVDD); also elsewhere on the board
VCC3V3: C95.2, C98.2, IC4.5 (V+), IC5.5 (V+), U$6.1 (IN), U$8.1 (IN), U$24.9 (SDI), U$24.10 (DVIO), U$25.9 (SDI), U$25.10 (DVIO), U$27.5 (V+), U$28.5 (V+); also elsewhere on the board
VREF: C22.1, R68.2, U$36.6 (VREF), U$36.7 (TERM_EN)

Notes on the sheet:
Charging circuit; (LiPos S2 7,4V 2400mAh); (Designed for 4 batteries)
1.8V
4.096V
2.5V
Inductor, Output Capacitance and Sense Resistor have now been estimated for a max. charge current of 6A: L = 4.7uH R_SR = 7.5mR C_o = 30uF (see table in 8.3.19 datasheet)
Resistor value calculated for a maximum charge current of 6A.
Resistor value calculated for a maximum current of 6A.
GMK325BJ226MM-P for 22u/35V CL32B106KLULNN for 10u/35V

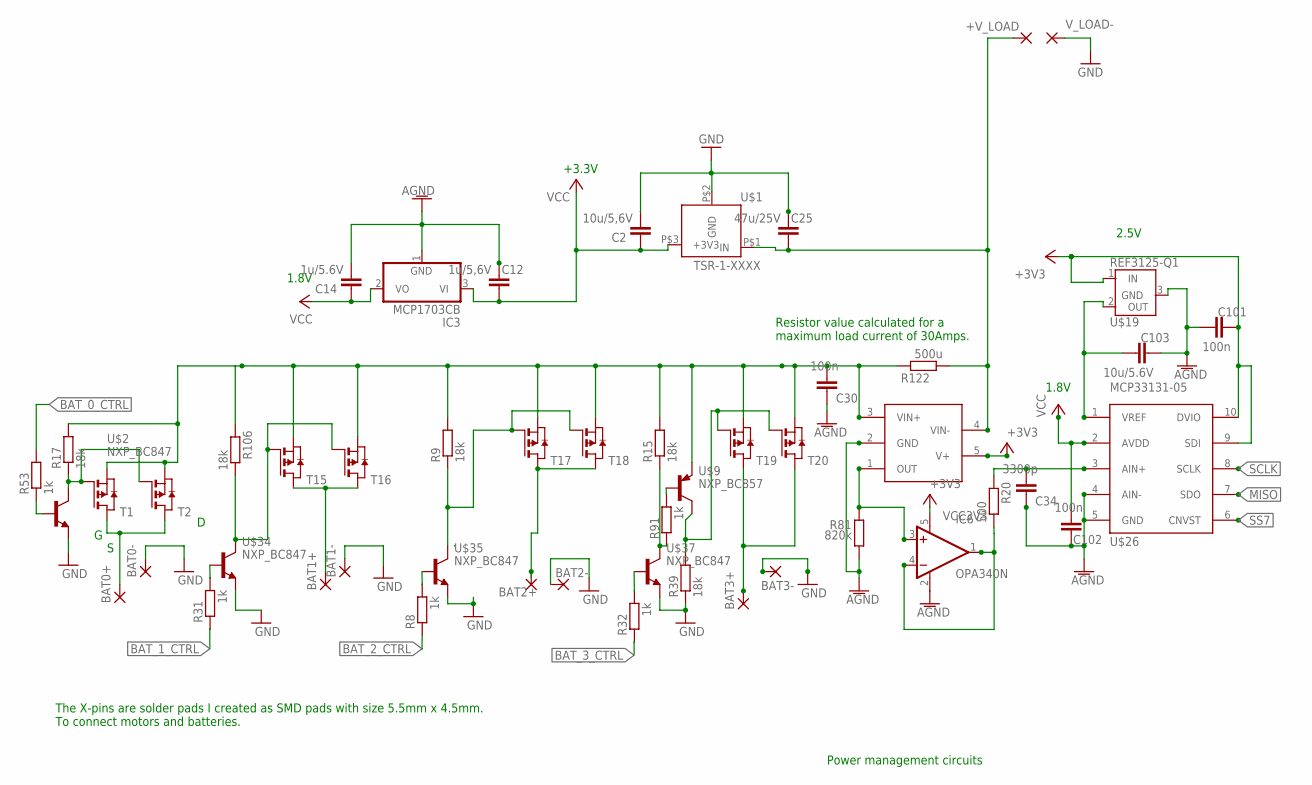
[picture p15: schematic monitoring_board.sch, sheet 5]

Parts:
+V_LOAD: SMDPAD
BAT0+, BAT0-, BAT1+, BAT1-, BAT2+, BAT2-, BAT3+, BAT3-: SMDPAD
C2: 10u/5,6V; C1206
C12: 1u/5,6V; C1206
C14: 1u/5.6V; C1206
C25: 47u/25V; C1206
C30, C101, C102: 100n; C0603
C34: 3300p; C0603
C103: 10u/5.6V; C0603
IC3: MCP1703CB; SOT23
IC6: OPA340N; SOT23-5
R8, R31, R32, R53, R91: 1k; R0603
R9, R15, R17, R39, R106: 18k; R0603
R20: 500; R0603
R81: 820k; R0603
R122: 500u; R2512
T1, T2, T15, T16, T17, T18, T19, T20: SI7157DP
U$1: TSR-1-XXXX
U$2, U$34, U$35, U$37: NXP_BC847
U$9: NXP_BC857
U$19: REF3125-Q1; REF31XX-Q1
U$26: MCP33131-05
U$29: INA138
V_LOAD-: SMDPAD

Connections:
+V_LOAD: +V_LOAD.1, C25.1, R122.1, U$1.P$1 (IN), U$29.4 (VIN-)
-V_LOAD: C30.2, R9.2, R15.2, R17.2, R106.2, R122.2, T1.1 (S), T1.2 (S), T1.3 (S), T2.1 (S), T2.2 (S), T2.3 (S), T15.1 (S), T15.2 (S), T15.3 (S), T16.1 (S), T16.2 (S), T16.3 (S), T17.1 (S), T17.2 (S), T17.3 (S), T18.1 (S), T18.2 (S), T18.3 (S), T19.1 (S), T19.2 (S), T19.3 (S), T20.1 (S), T20.2 (S), T20.3 (S), U$9.2 (E), U$29.3 (VIN+)
AGND: C12.2, C14.2, C30.1, C34.1, C101.1, C102.1, C103.2, IC3.1 (GND), IC6.2 (V-), R81.1, U$19.3 (GND), U$26.4 (AIN-), U$26.5 (GND), U$29.2 (GND); also elsewhere on the board
BAT0+: BAT0+.1, T1.5 (D), T1.6 (D), T1.7 (D), T1.8 (D), T1.9 (D), T2.5 (D), T2.6 (D), T2.7 (D), T2.8 (D), T2.9 (D); also elsewhere on the board
BAT1+: BAT1+.1, T15.5 (D), T15.6 (D), T15.7 (D), T15.8 (D), T15.9 (D), T16.5 (D), T16.6 (D), T16.7 (D), T16.8 (D), T16.9 (D); also elsewhere on the board
BAT2+: BAT2+.1, T17.5 (D), T17.6 (D), T17.7 (D), T17.8 (D), T17.9 (D), T18.5 (D), T18.6 (D), T18.7 (D), T18.8 (D), T18.9 (D); also elsewhere on the board
BAT3+: BAT3+.1, T19.5 (D), T19.6 (D), T19.7 (D), T19.8 (D), T19.9 (D), T20.5 (D), T20.6 (D), T20.7 (D), T20.8 (D), T20.9 (D); also elsewhere on the board
BAT_0_CTRL: R53.2; also elsewhere on the board
BAT_1_CTRL: R31.2; also elsewhere on the board
BAT_2_CTRL: R8.2; also elsewhere on the board
BAT_3_CTRL: R32.2; also elsewhere on the board
GND: BAT0-.1, BAT1-.1, BAT2-.1, BAT3-.1, C2.2, C25.2, R39.1, U$1.P$2 (GND), U$2.2 (E), U$34.2 (E), U$35.2 (E), U$37.2 (E), V_LOAD-.1; also elsewhere on the board
MISO: U$26.7 (SDO); also elsewhere on the board
unnamed: R106.1, T15.4 (G), T16.4 (G), U$34.3 (C)
unnamed: R9.1, T17.4 (G), T18.4 (G), U$35.3 (C)
unnamed: R91.1, U$9.1 (B)
unnamed: R8.1, U$35.1 (B)
unnamed: IC6.3 (+IN), R81.2, U$29.1 (OUT)
unnamed: R32.1, U$37.1 (B)
unnamed: R17.1, T1.4 (G), T2.4 (G), U$2.3 (C)
unnamed: IC6.1 (OUT), IC6.4 (-IN), R20.1
unnamed: R53.1, U$2.1 (B)
unnamed: R31.1, U$34.1 (B)
unnamed: R39.2, T19.4 (G), T20.4 (G), U$9.3 (C)
unnamed: C34.2, R20.2, U$26.3 (AIN+)
unnamed: R15.1, R91.2, U$37.3 (C)
unnamed: C103.1, U$19.2 (OUT), U$26.1 (VREF)
SCLK: U$26.8 (SCLK); also elsewhere on the board
SS7: U$26.6 (CNVST); also elsewhere on the board
VCC1V8: C14.1, C102.2, IC3.2 (VO), U$26.2 (AVDD); also elsewhere on the board
VCC3V3: C2.1, C12.1, C101.2, IC3.3 (VI), IC6.5 (V+), U$1.P$3 (+3V3), U$19.1 (IN), U$26.9 (SDI), U$26.10 (DVIO), U$29.5 (V+); also elsewhere on the board

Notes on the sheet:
1.8V
Power management circuits
+3.3V
Resistor value calculated for a maximum load current of 30Amps.
The X-pins are solder pads I created as SMD pads with size 5.5mm x 4.5mm. To connect motors and batteries.
2.5V

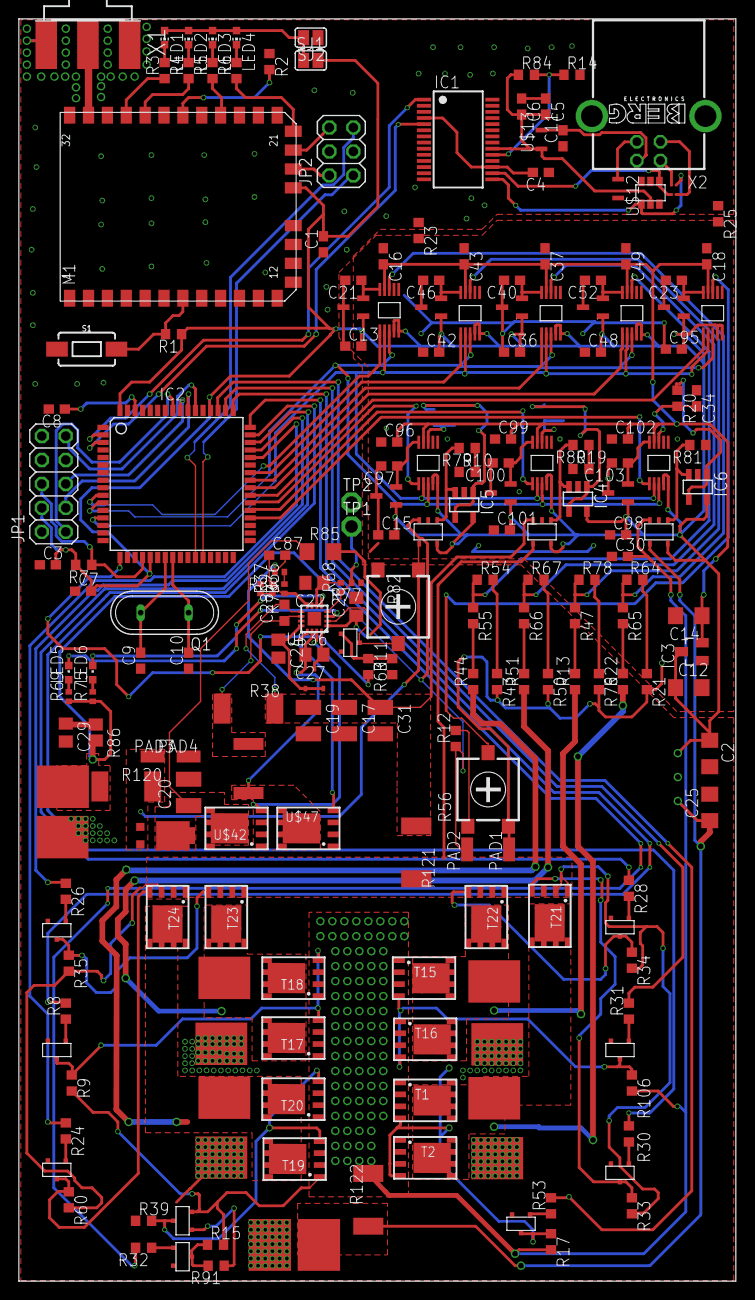
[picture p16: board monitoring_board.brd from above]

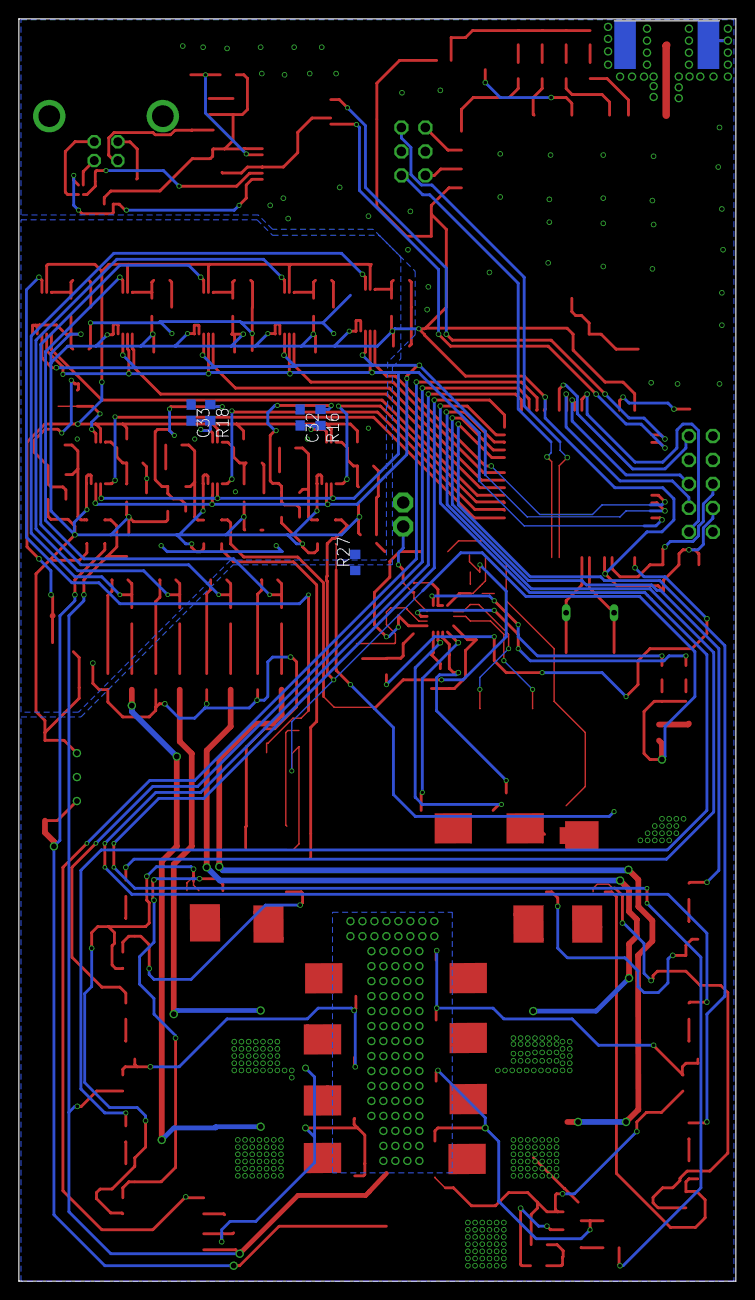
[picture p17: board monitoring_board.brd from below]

Board: 2 copper layers, 76.0 x 133.8 mm, 217 parts (5 on the bottom side), 139 nets.

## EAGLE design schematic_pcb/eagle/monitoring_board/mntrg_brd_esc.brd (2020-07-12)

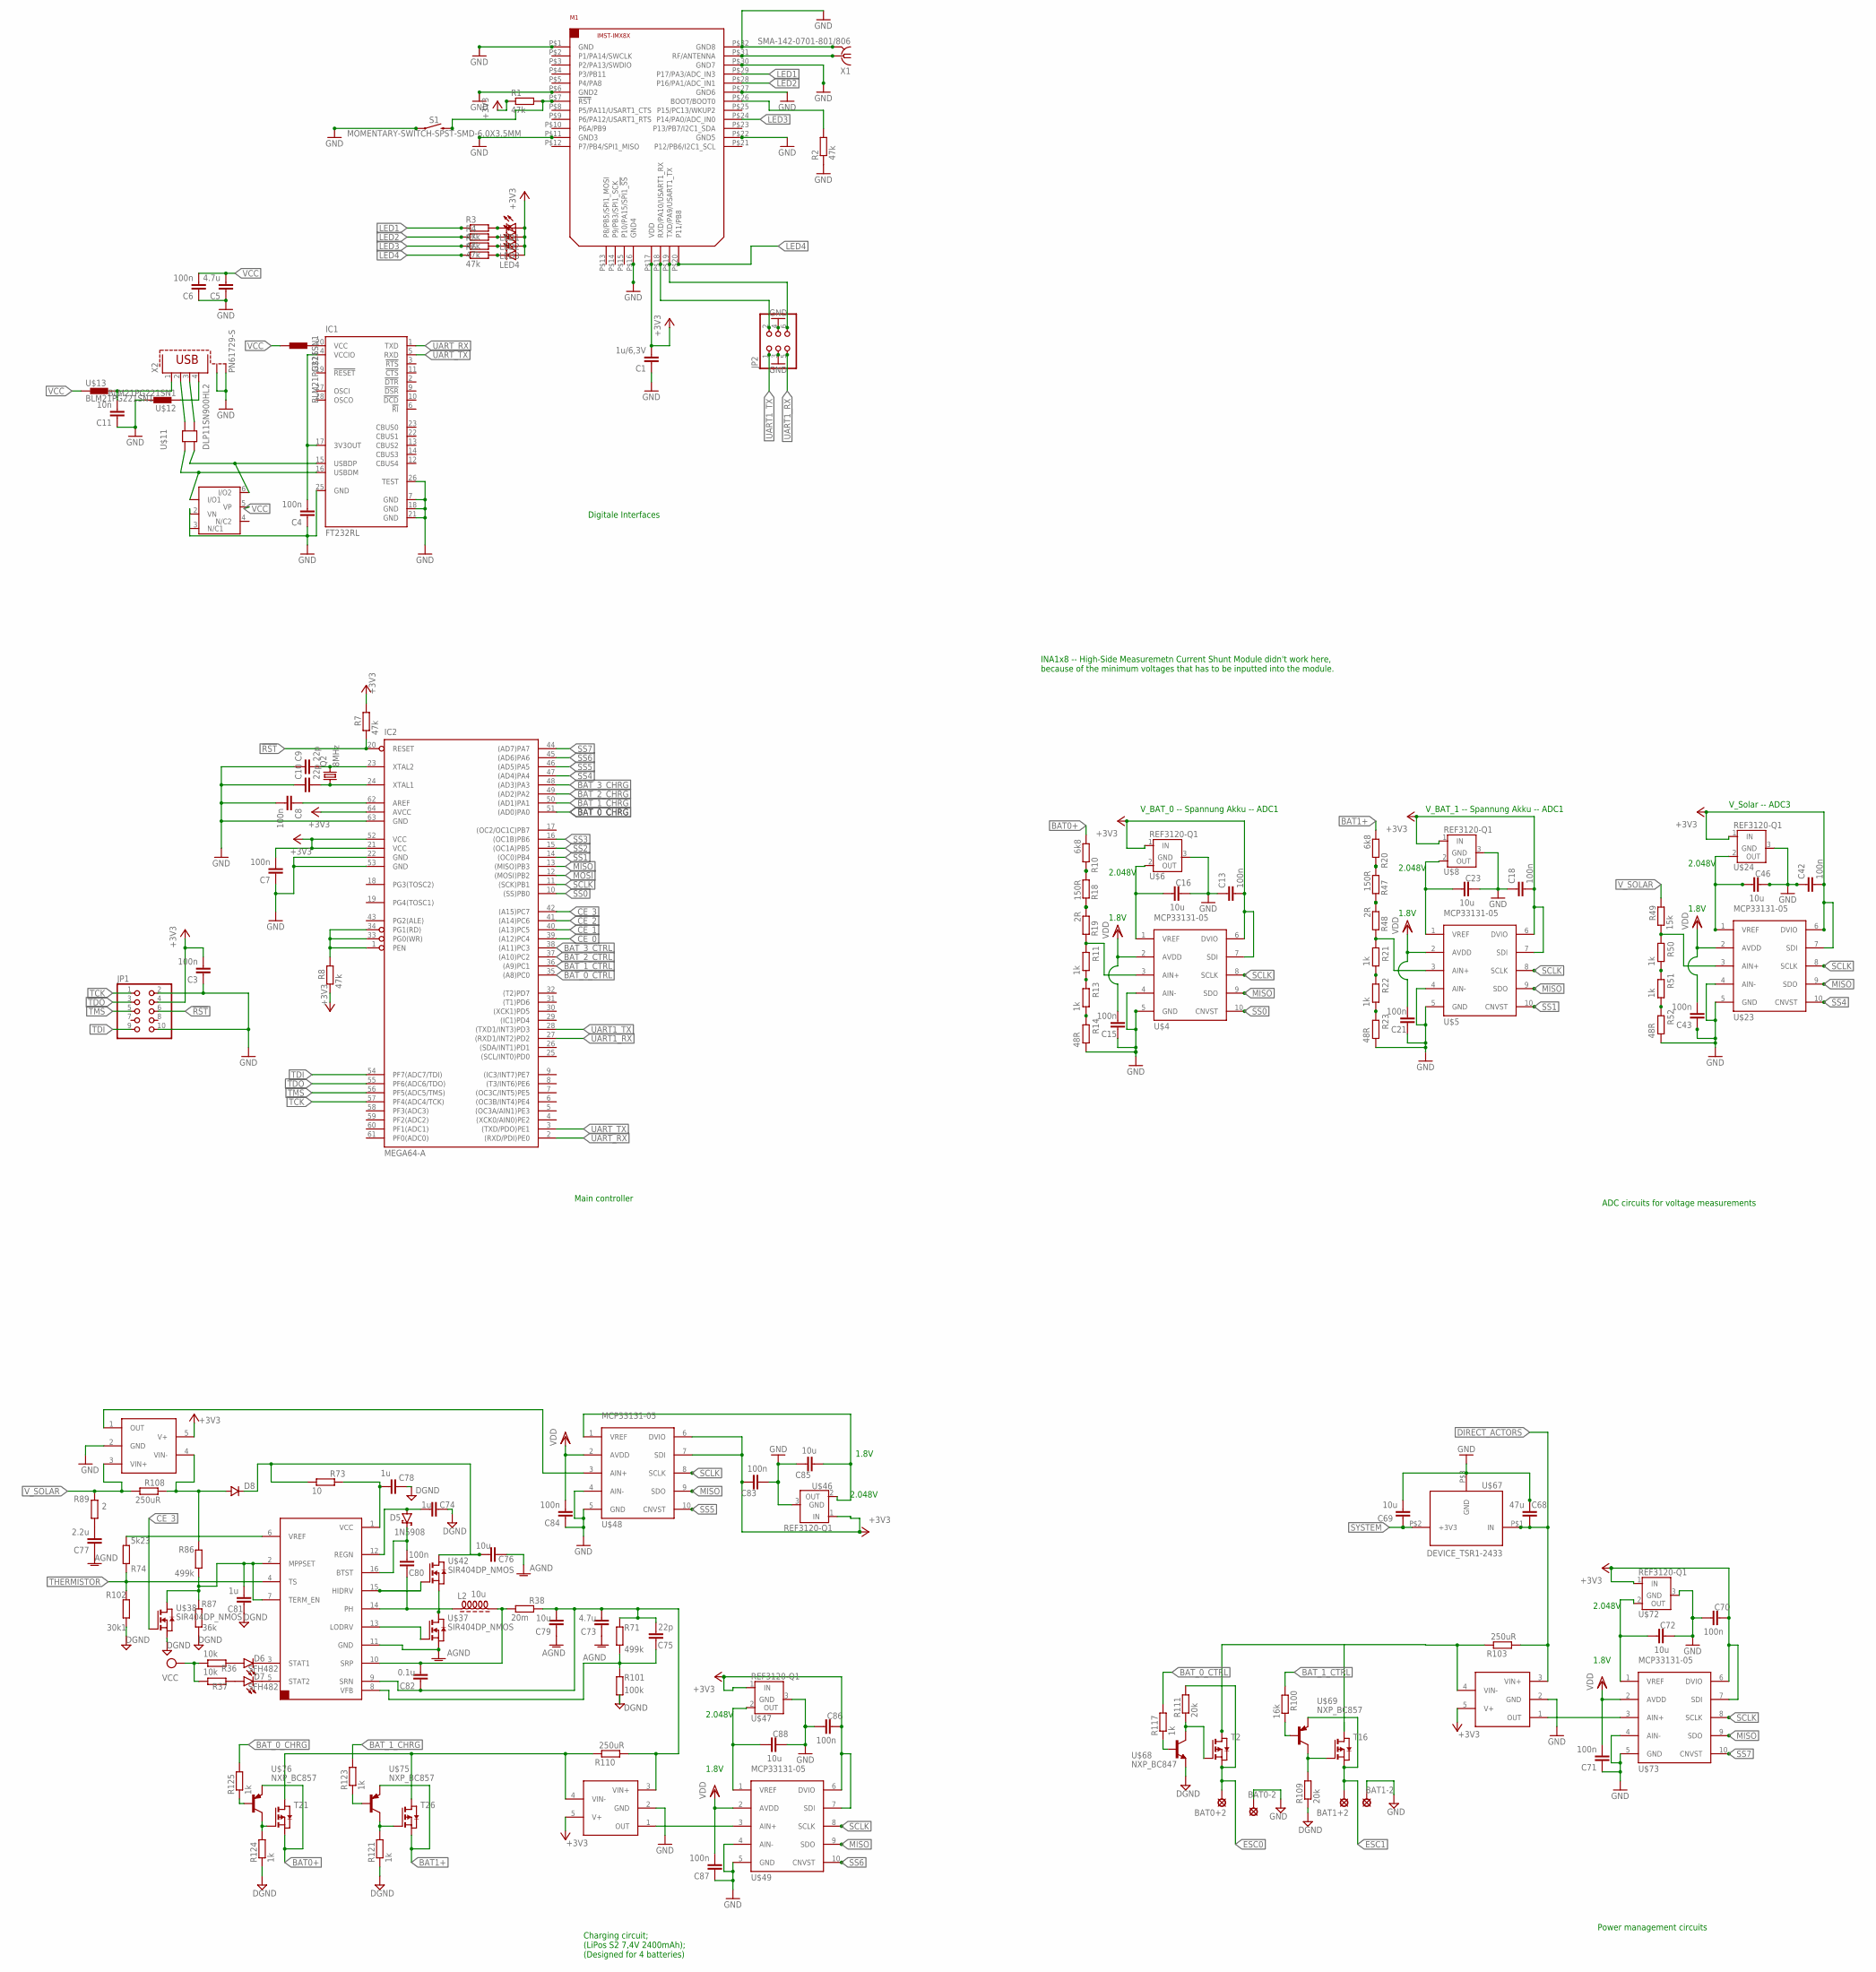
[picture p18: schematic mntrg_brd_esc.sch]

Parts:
BAT0+2, BAT0-2, BAT1+2, BAT1-2: SE14
C1: 1u/6,3V; C0603
C3, C4, C6, C7, C8, C13, C15, C18, C21, C42, C43, C70, C71, C80, C83, C84, C86, C87: 100n; C0603
C5, C73: 4.7u; C0603
C9, C10, C75: 22p; C0603
C11: 10n; C0603
C16, C23, C46, C72, C76, C79, C85, C88: 10u; C0603
C68: 47u; C1206
C69: 10u; C1206
C74, C78, C81: 1u; C0603
C77: 2.2u; C0603
C82: 0.1u; C0603
D5: 1N5908; C4111-15
D6, D7: SFH482
D8: VAR2SOT23; SOT-23
IC1: FT232RL; SSOP28
IC2: MEGA64-A; TQFP64
JP1: PINHD-2X5; 2X05
JP2: PINHD-2X3; 2X03
L2: 10u; Z15/1
LED1, LED2, LED3, LED4: LEDCHIP-LED0603; CHIP-LED0603
M1: IM-X8X
Q2: 8MHz; HC49/S
R1, R2, R3, R4, R5, R6, R7, R8: 47k; R0603
R10, R20: 6k8; R0603
R11, R13, R21, R22, R50, R51, R117, R121, R123, R124, R125: 1k; R0603
R14, R23, R52: 48R; R0603
R18, R47: 150R; R0603
R19, R48: 2R; R0603
R36, R37: 10k; R0603
R38: 20m; R0603
R49: 15k; R0603
R71, R86: 499k; R0603
R73: 10; R0603
R74: 5k23; R0603
R87: 36k; R0603
R89: 2; R0603
R100: 16k; R0603
R101: 100k; R0603
R102: 30k1; R0603
R103, R108, R110: 250uR; R0603
R109, R111: 20k; R0603
S1: MOMENTARY-SWITCH-SPST-SMD-6.0X3.5MM; TACTILE_SWITCH_SMD_6.0X3.5MM
T2, T16, T21, T26: SI7157DP_PMOS
U$4, U$5, U$23, U$48, U$49, U$73: MCP33131-05
U$6, U$8, U$24, U$46, U$47, U$72: REF3120-Q1
U$11: DLP11SN900HL2
U$12, U$13, U$15: BLM21PG221SN1
U$14: DUP2201MR6; NUP2201MR6
U$36: BQ24650
U$37, U$38, U$42: SIR404DP_NMOS
U$50, U$51, U$74: INA138
U$67: DEVICE_TSR1-2433; FOOTPRINT_TSR1-2344
U$68: NXP_BC847
U$69, U$75, U$76: NXP_BC857
X1: SMA-142-0701-801/806; J502-ND-142-0701-801/806
X2: PN61729-S

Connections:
!RST: IC2.20 (RESET), R7.1
+3V3: C1.2, C3.2, C7.2, C13.2, C18.2, C42.2, C70.2, C83.2, C86.2, IC2.21 (VCC), IC2.52 (VCC), IC2.64 (AVCC), JP1.4, LED1.A, LED2.A, LED3.A, LED4.A, M1.P$17 (VDD), R1.1, R7.2, R8.1, U$4.6 (DVIO), U$4.7 (SDI), U$5.6 (DVIO), U$5.7 (SDI), U$6.1 (IN), U$8.1 (IN), U$23.6 (DVIO), U$23.7 (SDI), U$24.1 (IN), U$46.1 (IN), U$47.1 (IN), U$48.6 (DVIO), U$48.7 (SDI), U$49.6 (DVIO), U$49.7 (SDI), U$50.5 (V+), U$51.5 (V+), U$72.1 (IN), U$73.6 (DVIO), U$73.7 (SDI), U$74.5 (V+)
AGND: C73.1, C76.1, C77.1, C79.1, U$36.11 (GND), U$37.1 (S), U$37.2 (S), U$37.3 (S)
BAT0+: R10.1, T21.1 (S), T21.2 (S), T21.3 (S), U$76.2 (E)
BAT1+: R20.1, T26.1 (S), T26.2 (S), T26.3 (S), U$75.2 (E)
BATTERY2: C73.2, C75.2, C79.2, C82.1, R38.2, R71.2, R110.1, U$36.9 (SRN), U$50.3 (VIN+)
BAT_0_CHRG: IC2.51 ((AD0)PA0), R125.2
BAT_0_CTRL: R117.2
BAT_1_CHRG: IC2.50 ((AD1)PA1), R123.2
BAT_1_CTRL: R100.2
BAT_2_CHRG: IC2.49 ((AD2)PA2)
BAT_3_CHRG: IC2.48 ((AD3)PA3)
CE_0: IC2.39 ((A12)PC4)
CE_1: IC2.40 ((A13)PC5)
CE_2: IC2.41 ((A14)PC6)
CE_3: U$38.4 (G)
DGND: C74.1, C78.1, C81.1, R87.1, R101.1, R102.1, R109.1, R121.1, R124.1, U$38.1 (S), U$38.2 (S), U$38.3 (S), U$68.2 (E)
DIRECT_ACTORS: C68.1, R103.1, U$67.P$1 (IN), U$74.3 (VIN+)
ESC0: BAT0+2.MP, R111.2, T2.1 (S), T2.2 (S), T2.3 (S)
ESC1: BAT1+2.MP, T16.1 (S), T16.2 (S), T16.3 (S), U$69.2 (E)
GND: BAT0-2.MP, BAT1-2.MP, C1.1, C3.1, C4.1, C5.1, C6.1, C7.1, C8.2, C9.1, C10.1, C11.1, C13.1, C15.1, C16.2, C18.1, C21.1, C23.2, C42.1, C46.2, C68.2, C69.2, C70.1, C71.1, C72.2, C83.1, C84.1, C85.2, C86.1, C87.1, C88.2, IC1.7 (GND), IC1.18 (GND), IC1.21 (GND), IC1.25 (GND), IC1.26 (TEST), IC2.22 (GND), IC2.53 (GND), IC2.63 (GND), JP1.2, JP1.10, JP2.3, JP2.4, M1.P$1 (GND), M1.P$6 (GND2), M1.P$11 (GND3), M1.P$16 (GND4), M1.P$22 (GND5), M1.P$27 (GND6), M1.P$30 (GND7), M1.P$32 (GND8), R2.1, R14.2, R23.2, S1.1, U$4.4 (AIN-), U$4.5 (GND), U$5.4 (AIN-), U$5.5 (GND), U$6.3 (GND), U$8.3 (GND), U$12.2, U$14.2 (VN), U$24.3 (GND), U$46.3 (GND), U$47.3 (GND), U$48.4 (AIN-), U$48.5 (GND), U$49.4 (AIN-), U$49.5 (GND), U$50.2 (GND), U$51.2 (GND), U$67.P$3 (GND), U$72.3 (GND), U$73.4 (AIN-), U$73.5 (GND), U$74.2 (GND), X1.G@1 (2), X1.G@2 (2), X1.G@3 (2), X1.G@4 (2), X2.S1, X2.S2
GND1: C43.1, R52.2, U$23.4 (AIN-), U$23.5 (GND)
LED1: M1.P$29 (P17/PA3/ADC_IN3), R3.1
LED2: M1.P$28 (P16/PA1/ADC_IN1), R4.1
LED3: M1.P$24 (P14/PA0/ADC_IN0), R5.1
LED4: M1.P$20 (P11/PB8), R6.1
MISO: IC2.13 ((MISO)PB3), U$4.9 (SDO), U$5.9 (SDO), U$23.9 (SDO), U$48.9 (SDO), U$49.9 (SDO), U$73.9 (SDO)
MOSI: IC2.12 ((MOSI)PB2)
unnamed: M1.P$31 (RF/ANTENNA), X1.1
unnamed: LED1.C, R3.2
unnamed: M1.P$7 (!RST), R1.2, S1.2
unnamed: M1.P$26 (BOOT/BOOT0), R2.2
unnamed: LED2.C, R4.2
unnamed: LED3.C, R5.2
unnamed: LED4.C, R6.2
unnamed: C9.2, IC2.23 (XTAL2), Q2.2
unnamed: C10.2, IC2.24 (XTAL1), Q2.1
unnamed: C8.1, IC2.62 (AREF)
unnamed: IC2.1 (PEN), IC2.33 (PG0(WR)), IC2.34 (PG1(RD)), R8.2
unnamed: U$11.2, X2.2
unnamed: U$11.4, X2.3
unnamed: IC1.16 (USBDM), U$11.1, U$14.1 (I/O1)
unnamed: IC1.15 (USBDP), U$11.3, U$14.6 (I/O2)
unnamed: U$12.1, X2.4
unnamed: C16.1, U$4.1 (VREF), U$6.2 (OUT)
unnamed: R11.1, R19.2, U$4.3 (AIN+)
unnamed: R13.2, R14.1
unnamed: C4.2, IC1.4 (VCCIO), IC1.17 (3V3OUT)
unnamed: R11.2, R13.1
unnamed: R10.2, R18.1
unnamed: C11.2, U$13.2, X2.1
unnamed: R18.2, R19.1
unnamed: C23.1, U$5.1 (VREF), U$8.2 (OUT)
unnamed: R21.1, R48.2, U$5.3 (AIN+)
unnamed: R22.2, R23.1
unnamed: R21.2, R22.1
unnamed: R20.2, R47.1
unnamed: R47.2, R48.1
unnamed: C77.2, R89.1
unnamed: R74.1, U$36.6 (VREF)
unnamed: C81.2, R86.1, R87.2, U$36.2 (MPPSET), U$36.7 (TERM_EN)
unnamed: D6.K (C), U$36.3 (STAT1)
unnamed: D7.K (C), U$36.5 (STAT2)
unnamed: D6.A, R36.2
unnamed: D7.A, R37.2
unnamed: C46.1, U$23.1 (VREF), U$24.2 (OUT)
unnamed: R49.1, R50.1, U$23.3 (AIN+)
unnamed: R51.2, R52.1
unnamed: R50.2, R51.1
unnamed: C78.2, R73.2, U$36.1 (VCC)
unnamed: C74.2, D5.A, U$36.12 (REGN)
unnamed: C80.1, L2.1, U$36.14 (PH)
unnamed: C82.2, L2.2, R38.1, U$36.10 (SRP)
unnamed: C80.2, D5.C, U$36.16 (BTST)
unnamed: U$36.15 (HIDRV), U$42.4 (G)
unnamed: C76.2, D8.1 (C), R73.1, U$42.5 (D), U$42.6 (D), U$42.7 (D), U$42.8 (D)
unnamed: C75.1, R71.1, R101.2, U$36.8 (VFB)
unnamed: C72.1, U$72.2 (OUT), U$73.1 (VREF)
unnamed: U$73.3 (AIN+), U$74.1 (OUT)
unnamed: R103.2, T2.5 (D), T2.6 (D), T2.7 (D), T2.8 (D), T16.5 (D), T16.6 (D), T16.7 (D), T16.8 (D), U$74.4 (VIN-)
unnamed: R111.1, T2.4 (G), U$68.3 (C)
unnamed: R117.1, U$68.1 (B)
unnamed: R109.2, T16.4 (G), U$69.3 (C)
unnamed: D8.3 (A), R86.2, R108.2, U$51.4 (VIN-)
unnamed: U$38.5 (D), U$38.6 (D), U$38.7 (D), U$38.8 (D)
unnamed: U$37.5 (D), U$37.6 (D), U$37.7 (D), U$37.8 (D), U$42.1 (S), U$42.2 (S), U$42.3 (S)
unnamed: R100.1, U$69.1 (B)
unnamed: C88.1, U$47.2 (OUT), U$49.1 (VREF)
unnamed: R110.2, T21.5 (D), T21.6 (D), T21.7 (D), T21.8 (D), T26.5 (D), T26.6 (D), T26.7 (D), T26.8 (D), U$50.4 (VIN-)
unnamed: U$49.3 (AIN+), U$50.1 (OUT)
unnamed: C85.1, U$46.2 (OUT), U$48.1 (VREF)
unnamed: U$48.3 (AIN+), U$51.1 (OUT)
unnamed: R124.2, T21.4 (G), U$76.3 (C)
unnamed: R125.1, U$76.1 (B)
unnamed: R121.2, T26.4 (G), U$75.3 (C)
unnamed: R123.1, U$75.1 (B)
SCLK: IC2.11 ((SCK)PB1), U$4.8 (SCLK), U$5.8 (SCLK), U$23.8 (SCLK), U$48.8 (SCLK), U$49.8 (SCLK), U$73.8 (SCLK)
SS0: IC2.10 ((SS)PB0), U$4.10 (CNVST)
SS1: IC2.14 ((OC0)PB4), U$5.10 (CNVST)
SS2: IC2.15 ((OC1A)PB5)
SS3: IC2.16 ((OC1B)PB6)
SS4: IC2.47 ((AD4)PA4), U$23.10 (CNVST)
SS5: IC2.46 ((AD5)PA5), U$48.10 (CNVST)
SS6: IC2.45 ((AD6)PA6), U$49.10 (CNVST)
SS7: IC2.44 ((AD7)PA7), U$73.10 (CNVST)
SYSTEM: C69.1, U$67.P$2 (+3V3)
TCK: JP1.1
TDI: JP1.9
TDO: JP1.3
THERMISTOR: R74.2, R102.2, U$36.4 (TS)
TMS: JP1.5
UART1_RX: IC2.27 ((RXD1/INT2)PD2), JP2.5, JP2.6, M1.P$19 (TXD/PA9/USART1_TX)
UART1_TX: IC2.28 ((TXD1/INT3)PD3), JP2.1, JP2.2, M1.P$18 (RXD/PA10/USART1_RX)
UART_RX: IC1.1 (TXD), IC2.2 ((RXD/PDI)PE0)
UART_TX: IC1.5 (RXD), IC2.3 ((TXD/PDO)PE1)
VCC: C5.2, C6.2, IC1.20 (VCC), R36.1, R37.1, U$13.1, U$14.5 (VP), U$15.1, U$15.2
VDD: C15.2, C21.2, C43.2, C71.2, C84.2, C87.2, U$4.2 (AVDD), U$5.2 (AVDD), U$23.2 (AVDD), U$48.2 (AVDD), U$49.2 (AVDD), U$73.2 (AVDD)
V_SOLAR: R49.2, R89.2, R108.1, U$51.3 (VIN+)

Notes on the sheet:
ADC circuits for voltage measurements
Main controller
Digitale Interfaces
INA1x8 -- High-Side Measuremetn Current Shunt Module didn't work here, because of the minimum voltages that has to be inputted into the module.
Charging circuit; (LiPos S2 7,4V 2400mAh); (Designed for 4 batteries)
Power management circuits
1.8V
2.048V
V_BAT_0 -- Spannung Akku -- ADC1
V_BAT_1 -- Spannung Akku -- ADC1
V_Solar -- ADC3

Board: 2 copper layers, 141 parts (0 on the bottom side), 103 nets, no tracks yet.

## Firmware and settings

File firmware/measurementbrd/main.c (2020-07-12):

/*
 * main.c
 *
 * Created: 23.01.2020 12:35:42
 * Author : Patrick Lodes
 */ 

#include "main.h"

/* ----------------------- Ringbuffer for serial communication -----------------------------*/
#include "ringbuffer.h"

/* ----------------------- UART communication -----------------------------*/
#include "UART/UART0.h"
#include "UART/UART1.h"

/* ----------------------- SPI communication -----------------------------*/
#include "SPI.h"

/* ----------------------- LoRa Wireless Interface -----------------------------*/
#include "WiMOD/WiMOD_HCI_Layer.h"
#include "WiMOD_HCI_Host.h"

/* ----------------------- MODBUS libraries -----------------------------*/
#include "modbus/include/mb.h"
#include "modbus/include/mbport.h"

/* ----------------------- AVR libraries -----------------------------*/
#include <avr/interrupt.h>
#include <avr/io.h>

/* ----------------------- Standard C -----------------------------*/
#include <util/delay.h>
#include <stdio.h>



/* ----------------------- Defines MODBUS------------------------------------------*/
// Input Registers allocation:
// 	[0] - Volts Bat0
// 	[1] - Volts Bat1
// 	[2] - Volts Bat2
// 	[3] - Volts Bat3
// 	[4] - Volts Solar
// 	[5] - Current Solar
// 	[6] - Current Charge
// 	[7] - Current Load
// 	[8] - ActiveFlag
// 	[9] - ChargeFlag
#define REG_INPUT_START 30000
#define REG_INPUT_NREGS 10

// Holding Registers allocation:
// 	[0] - Operation Mode
// 	[1] - # Bats
// 	[2] - # Cells per Bat (fixed for now)
// 	[3] - Active Bat (Only if MANUAL_MODE)
//  [4] - Chrgng Bat (Only if MANUAL_MODE)
#define REG_HOLDING_START 40000
#define REG_HOLDING_NREGS 9


/* ----------------------- Static variables MODBUS ---------------------------------*/
// Input Registers
static USHORT   usRegInputStart = REG_INPUT_START;
static USHORT   usRegInputBuf[REG_INPUT_NREGS];
// Holding Registers 
static USHORT   usRegHoldingStart = REG_HOLDING_START;
static USHORT   usRegHoldingBuf[REG_HOLDING_NREGS];

/* ---------- MODBUS dynamic variables used for MODBUS initialization ---------- */
// Slave characteristics
static eMBMode MB_MODE = MB_RTU;
static UCHAR SLAVE_ADDRESS = 0x0A; // Decimal: 10
static UCHAR PORT = 0;
static ULONG BAUDRATRE = 115200;  
static eMBParity PARITY = MB_PAR_NONE;

const UCHAR     ucSlaveID[] = { 0xAA, 0xBB, 0xCC };
eMBErrorCode    eStatus;


/* ----------------------- Variables Timer 0: For Fetching ADC data ---------------------------------*/
// Prescaler of 1024:	t_interval = ( 2^8 * 1024 ) / 7372800 = 0.036s
// So 28 timer overflows in the second
// For an interval of 1s we react only every 28th interrupt
#define ADC_TIMER_OVF_FACTOR				28	 
volatile uint8_t adc_timer_ovf_cnt;
// For an interval of 4s we react only every 56th interrupt
#define WIMOD_TIMER_OVF_FACTOR				224	//	112
volatile uint16_t wimod_timer_ovf_cnt;


/* ----------- Control pins for battery management ------------ */
// ATTENTION: The batteries indices used in firmware are not directly matching 
// 			  the indices of the controller pins.
// Index-translations:
// Ctrl:   FW   |   HW 		  ||	Chrg: 	FW	 |   HW
//          0	|	PA3       ||			 0   |   PA7
// 			1   |   PA0       ||			 1   |   PA4
// 			2   |   PA2       || 			 2   |   PA6
// 			3   |	PA1       ||			 3   |   PA5

#define BAT_0_CTRL 					PA3		// Default: Conducting
#define BAT_1_CTRL					PA0		// Default: Non-Conducting
#define BAT_2_CTRL  				PA2		// Default: Non-Conducting		
#define BAT_3_CTRL  				PA1		// Default: Non-Conducting

#define BAT_0_CHRG  				PA7		// Default: Non-Conducting
#define BAT_1_CHRG  				PA4		// Default: Non-Conducting
#define BAT_2_CHRG  				PA6		// Default: Non-Conducting
#define BAT_3_CHRG  				PA5		// Default: Non-Conducting

/* ------- Management mode -------- */
#define NUM_2_BAT						2
#define NUM_3_BAT						3		// 15277
#define NUM_4_BAT						4		// 19373

/* ------------------------ Number of battery cells ------------------------------- */
#define BAT_CELLS					2

//* ----------------------- Voltage limits of charging ---------------------------- */
// Values from here: https://de.wikipedia.org/wiki/Lithium-Polymer-Akkumulator
// Per cell:
// 		Min: 3.3v			(Cutoff voltage - Entladeschlussspannung)
//		Max: 4.0v to 4.2v	(End-of-Charge voltage - Ladeschlussspannung)
//
// NOTE: voltage values represented as scaled value between 0 and 65536 from ADC
#if BAT_CELLS == 2
#define BAT_MIN_VOLTS				48907 		// Margin of 0.05: U_adc_scaled = (6.6 + 0.05) / C_volt_divider * C_adc_scale
#define BAT_MAX_VOLTS				61410		// Margin of 0.05: U_adc_scaled = (8.4 - 0.05) / C_volt_divider * C_adc_scale
#endif

/* 
 T.b.d. Different voltage dividers required i.e. the constant for the divider differs.
#elif BAT_CELLS == 3
#define BAT_MIN_VOLTS				9.9 + 0.05				
#define BAT_MAX_VOLTS				12.6 - 0.05

#elif BAT_CELLS == 4
#define BAT_MIN_VOLTS				13.2 + 0.05				
#define BAT_MAX_VOLTS				16.8 - 0.05
#endif

/* ------- Constants for "Rest" times in 3-Bat system ------- */
// Simple strategy:
// As the voltage of lithium-ion batteries has a plateau somewhere between
// 80% (and 20%) we just use exactly these limits to start charging.
// https://www.quora.com/How-does-a-smartphone-measure-battery-capacity-when-the-voltage-is-constant-from-20-to-80

// This FACTOR reduces the "rest time" automatically (when using a smaller then premise)
// as the SOC sinks because batteries might not have been fully charged.

// To find the right factor some calculations or fine-tuning will be useful.
//#if NUM_BATS == _3_BAT
#define SOC_INIT_CHRG				0.9
//#endif


/* ----------------------- Flags for status in battery management ---------------------------------*/
/*typedef USHORT ActiveFlag, 
			   ChargeFlag; */

const uint16_t STAT_ACT_B0 = 		0x0000;
const uint16_t STAT_ACT_B1 =		0x0001;
const uint16_t STAT_ACT_B2 =		0x0002;
const uint16_t STAT_ACT_B3 =		0x0003;
const uint16_t STAT_ACT_NONE =		0xbabe;

const uint16_t STAT_CHRG_B0 =		0x0004;
const uint16_t STAT_CHRG_B1 =		0x0005;
const uint16_t STAT_CHRG_B2 =		0x0006;
const uint16_t STAT_CHRG_B3	=		0x0007;
const uint16_t STAT_CHRG_NONE =		0xbabe;

uint16_t *bat_active = &usRegInputBuf[8];
uint16_t *bat_chrgng = &usRegInputBuf[9];


/************************************************************************/
/* MODE SETTINGS                                                        */
/************************************************************************/
bool *MANUAL_MODE			=	&usRegHoldingBuf[0];
uint16_t *NUM_BATS			=	&usRegHoldingBuf[1];
// uint16_t BAT_CELLS = 2; see above
uint16_t *next_bat_active	=   &usRegHoldingBuf[3];
uint16_t *next_bat_chrgng   =   &usRegHoldingBuf[4];
bool *WIRELESS_MODE			=   &usRegHoldingBuf[5];	// 0 - Communication via MODBUS; 1 - Communication via WiMOD
bool *NEW_SETTINGS			=   &usRegHoldingBuf[6];
bool *CHRG_CYCLE			=   &usRegHoldingBuf[7];
bool *EMERGENCY_STOP		=   &usRegHoldingBuf[8];



/* ---------- Fetches ADC values per SPI ---------- */
// ATTENTION: The batteries indices used in firmware are not directly matching 
// 			  the indices of the controller pins.
// Index-translations:
// Ctrl:   FW   |   HW 
//          0	|	SS3
// 			1   |   SS0
// 			2   |   SS2
// 			3   |	SS1
void fetch_adc_values(void){
	usRegInputBuf[0] = spi_rx16_adc_portc(DD_SS3);	// Volts Bat0
	usRegInputBuf[1] = spi_rx16_adc_portb(DD_SS0);	// Volts Bat1
	usRegInputBuf[2] = spi_rx16_adc_portc(DD_SS2);	// Volts Bat2
	usRegInputBuf[3] = spi_rx16_adc_portc(DD_SS1);  // Volts Bat3
	usRegInputBuf[4] = spi_rx16_adc_portc(DD_SS4);  // Volts Solar

	usRegInputBuf[5] = spi_rx16_adc_portc(DD_SS5);  // Current Solar
	usRegInputBuf[6] = spi_rx16_adc_portc(DD_SS6);  // Current Charge
	usRegInputBuf[7] = spi_rx16_adc_portc(DD_SS7);  // Current Load
}

USHORT get_volts_bat(USHORT index)
{
	return usRegInputBuf[(index % 4)];
}

USHORT get_volts_next_bat(USHORT index)
{
	switch(*NUM_BATS)
	{
		case NUM_2_BAT:
		return usRegInputBuf[((index + 1) % NUM_2_BAT)];
		//break;
		case NUM_3_BAT:
		return usRegInputBuf[((index + 1) % NUM_3_BAT)];
		//break;
		case NUM_4_BAT:
		return usRegInputBuf[((index + 1) % NUM_4_BAT)];
		//break;
		default:
		// Kaesekuchen
		break;
	}
}
	

USHORT get_volts_active_bat(void)
{
	return usRegInputBuf[usRegInputBuf[8]];
}

USHORT get_volts_charge_bat(void)
{
	return usRegInputBuf[usRegInputBuf[9] % 4];
}

/**
 * Checks whether batteries are {connected|!damaged}. 
 */ 
bool assert_bats_ok(void){
	switch(*NUM_BATS){
		case NUM_2_BAT:
			return (usRegInputBuf[0] >= BAT_MIN_VOLTS && usRegInputBuf[0] <= BAT_MAX_VOLTS)
				&& (usRegInputBuf[1] >= BAT_MIN_VOLTS && usRegInputBuf[1] <= BAT_MAX_VOLTS);
		case NUM_3_BAT:
			return (usRegInputBuf[0] >= BAT_MIN_VOLTS && usRegInputBuf[0] <= BAT_MAX_VOLTS)
				&& (usRegInputBuf[1] >= BAT_MIN_VOLTS && usRegInputBuf[1] <= BAT_MAX_VOLTS)
				&& (usRegInputBuf[2] >= BAT_MIN_VOLTS && usRegInputBuf[2] <= BAT_MAX_VOLTS);
		case NUM_4_BAT:
			return (usRegInputBuf[0] >= BAT_MIN_VOLTS && usRegInputBuf[0] <= BAT_MAX_VOLTS)
				&& (usRegInputBuf[1] >= BAT_MIN_VOLTS && usRegInputBuf[1] <= BAT_MAX_VOLTS)
				&& (usRegInputBuf[2] >= BAT_MIN_VOLTS && usRegInputBuf[2] <= BAT_MAX_VOLTS)
				&& (usRegInputBuf[3] >= BAT_MIN_VOLTS && usRegInputBuf[3] <= BAT_MAX_VOLTS);
		default:
			return false;
	}

}

bool assert_charge_source_connected(void){
	// Check for a sensible value to garantuee that energy source for charging is connected.
}

void stop_chargng_bat(void){
	switch(*bat_chrgng){
		case (uint16_t) STAT_CHRG_B0:
			PORTA &= ~(1 << BAT_0_CHRG);
		break;
		case (uint16_t) STAT_CHRG_B1:
			PORTA &= ~(1 << BAT_1_CHRG);
		break;
		case (uint16_t) STAT_CHRG_B2:
			PORTA &= ~(1 << BAT_2_CHRG);
		break;
		case (uint16_t) STAT_CHRG_B3:
			PORTA &= ~(1 << BAT_3_CHRG);
		break;
		default:
		break;

		*bat_chrgng = STAT_CHRG_NONE;
	}
}

/**
 * Routine for energy management with 2 batteries
 *     | Init  | Cycle  |  1   |  2   |  3   |  4   | ..
 *	B0 | Fly   | Chrg   | Fly  | Chrg | Fly  | Chrg | .. 
 *  B1 | ----  | Fly    | Chrg | Fly  | Chrg | Fly  | ..
 */
//#if NUM_BATS == _2_BAT
void manage_2_BAT(void)
{
	if(*CHRG_CYCLE == false){
		if((float) get_volts_bat(*bat_active) <= BAT_MIN_VOLTS){
			// Check whether next battery is above its minimum State of charge
			if((float) get_volts_next_bat(*bat_active) <= BAT_MIN_VOLTS)
			{
				*EMERGENCY_STOP = true;
				return;
			}
			
			switch(usRegInputBuf[8]){
				case (uint16_t) STAT_ACT_B0:
					PORTA |= (1 << BAT_0_CTRL);		// PULL-UP!!  
					PORTA |= (1 << BAT_1_CTRL);
					// Charge Bat 0
					PORTA |= (1 << BAT_0_CHRG);

					// Update the indices here.
					usRegInputBuf[8] = STAT_ACT_B1;
					usRegInputBuf[9] = STAT_CHRG_B0;

					*CHRG_CYCLE = true;			/* Enable charge cycle */
				break;
				case (uint16_t) STAT_ACT_B1:
					// Should not happen..
				break;
				default:
				break;
			}

		}
	}else{
		if((float) get_volts_bat(*bat_active) <= BAT_MIN_VOLTS){
			// Check whether next battery is above its minimum State of charge
			if((float) get_volts_next_bat(*bat_active) <= BAT_MIN_VOLTS)
			{
				*EMERGENCY_STOP = true;
				return;
			}
			
			switch(usRegInputBuf[8]){
				case (uint16_t) STAT_ACT_B0:
					// (Dis)Active charging Bat 1
					PORTA &= ~(1 << BAT_1_CHRG);
					// (Dis)Activate Bat-(0)1
					PORTA |= (1 << BAT_0_CTRL);		// PULL-UP!! 
					PORTA |= (1 << BAT_1_CTRL);
					// Charge Bat 0
					PORTA |= (1 << BAT_0_CHRG);

					// Update the indices here.
					usRegInputBuf[8] = STAT_ACT_B1;
					usRegInputBuf[9] = STAT_CHRG_B0;
				break;
				case (uint16_t) STAT_ACT_B1:
					// (Dis)Active charging Bat 0
					PORTA &= ~(1 << BAT_0_CHRG);
					// (Dis)Activate Bat-(1)0
					PORTA &= ~(1 << BAT_1_CTRL); 
					PORTA &= ~(1 << BAT_0_CTRL);  	// PULL-UP!! 
					// Charge Bat 1
					PORTA |= (1 << BAT_1_CHRG);

					// Update the indices here.
					usRegInputBuf[8] = STAT_ACT_B0;
					usRegInputBuf[9] = STAT_CHRG_B1;
				break;

				default:
					// Should not happen..
				break;
			}	
		}else{		/* Check that charging battery is ok. */

			if((float) get_volts_bat(*bat_chrgng) >= BAT_MAX_VOLTS){
				stop_chargng_bat( );
			}
		}
	}
}
//#endif

/**
 *  Routine for energy management with 3 batteries
 *     | Init |   |   1  |  2   |  3   |  4   |  5   |  5   |  6   | ..
 *	B0 | Fly  | R | Chrg | R| Fly  | R | Chrg | R | Fly  |R | Ch..
 *  B1 | ---- | Fly  | R | Chrg | R | Fly  |R | Chrg | R | Fly  | .. 
 *  B2 | ---- | ---- | Fly  | R | Chrg | R | Fly | R | Chrg | R | .. 
 */
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
int main(void)
{

    /* Initialize routine.. */
	init_all();
	
	//some_testing_stuff( ); 
	//send_system_info_radio();
	

	config_lora_module();

	while(1)
	{
		/* ---- Check whether batteries are ok. ---- */
		if(assert_bats_ok( )){		// if not break the control loop.
				
			/************************************************************************************************/
			/*	Something is not okay with batteries so best would be to completely cut the					*/
			/*	connection!!! But This doesn't work as the MOSFET for Bat0 would be automatically switched  */
			/*	back on on power loss!!!																	*/
			/*	Responsibility lays in the hands of the experiment conductor.								*/
			/************************************************************************************************/
				
			*EMERGENCY_STOP = false;
		}else{
			*EMERGENCY_STOP = true;
		}

		cli();
		// Every 1s -- Fetch system data and do energy management
		if(adc_timer_ovf_cnt == ADC_TIMER_OVF_FACTOR)
		{		
			// Reset overflow counter
			adc_timer_ovf_cnt = 0;

			// Update ADC values
			fetch_adc_values( );
				
			/* ---------- Execute battery management routine ---------- */
// 				if(*MANUAL_MODE == false)
// 				{
// 					energy_management( );
// 				}

					
		}
		sei();

			
		cli();
		if(wimod_timer_ovf_cnt == WIMOD_TIMER_OVF_FACTOR)
		{
			wimod_timer_ovf_cnt = 0;
				
			send_system_info_radio();	
		}
		sei();
			
		/* ---------- Cyclical polling.. ---------- */
		/*
		if(*WIRELESS_MODE)
		{
			// .. the LoRa interface
			cli();
			if(BufferCount() > 0)
				WiMOD_HCI_ATmega64_Process( );
			sei();
		}
		else
		{
			// .. or the MODBUS 
			( void )eMBPoll( );
		}
		*/
			
		// .. or the MODBUS 
		( void )eMBPoll( );

 		if(*EMERGENCY_STOP == false && *MANUAL_MODE == false)
 		{
 			energy_management( );
		}
		else if(*MANUAL_MODE && *NEW_SETTINGS)
		{
			// Activate new settings fetched from holding registers...
			manual_set_active();
			manual_set_chrgng();
				
			*NEW_SETTINGS = false;
		}
			
	}
}

void manual_set_active(void){
	// Set all batteries to null (spares a switch statement, considering I don't want to refactor my 
	// data structures..)
	PORTA &= ~( (1 << BAT_3_CTRL) | (1 << BAT_2_CTRL) | (1 << BAT_1_CTRL) | (1 << BAT_0_CTRL));
	switch(*next_bat_active){
		case (uint16_t) STAT_ACT_B0:
			// Activate B0
			PORTA &= ~(1 << BAT_0_CTRL);		// PULL-UP
			*bat_active = STAT_ACT_B0;
		break;
		case (uint16_t) STAT_ACT_B1:
		// Activate B1
			PORTA |= (1 << BAT_1_CTRL);
			*bat_active = STAT_ACT_B1;
		break;
		case (uint16_t) STAT_ACT_B2:
			// Activate B2
			PORTA |= (1 << BAT_2_CTRL);
			*bat_active = STAT_ACT_B2;
		break;
		case (uint16_t) STAT_ACT_B3:
			// Activate B3
			PORTA |= (1 << BAT_3_CTRL);
			*bat_active = STAT_ACT_B3;
		break;
		case (uint16_t) STAT_ACT_NONE:
			// No battery charging..
			*bat_active = STAT_ACT_NONE;
		default:
		break;
	}	
}

void manual_set_chrgng(void){
	// Set all batteries to null (spares a switch statement, considering I don't want to refactor my 
	// data structures..)
	PORTA &= ~( (1 << BAT_3_CHRG) | (1 << BAT_2_CHRG) | (1 << BAT_1_CHRG) | (1 << BAT_0_CHRG));
	switch(*next_bat_chrgng){
		case (uint16_t) STAT_CHRG_B0:
			// Activate charging B0
			PORTA |= (1 << BAT_0_CTRL);
			*bat_chrgng = STAT_CHRG_B0;
		break;
		case (uint16_t) STAT_CHRG_B1:
		// Activate charging B1
			PORTA |= (1 << BAT_1_CHRG);
			*bat_chrgng = STAT_CHRG_B1;
		break;
		case (uint16_t) STAT_CHRG_B2:
			// Activate charging B2
			PORTA |= (1 << BAT_2_CHRG);
			*bat_chrgng = STAT_CHRG_B2;
		break;
		case (uint16_t) STAT_CHRG_B3:
			// Activate charging B3
			PORTA |= (1 << BAT_3_CHRG);
			*bat_chrgng = STAT_CHRG_B3;
		break;
		case (uint16_t) STAT_CHRG_NONE:
			// No battery charging..
			*bat_chrgng = STAT_CHRG_NONE;
		default:
		break;
	}
}

void settings_to_holding(void)
{
	/* --- Write settings to holding registers --- */
	usRegHoldingBuf[0] = (int16_t) MANUAL_MODE;
	usRegHoldingBuf[1] = (int16_t) NUM_BATS;
	usRegHoldingBuf[2] = (int16_t) BAT_CELLS;
	usRegHoldingBuf[3] = (int16_t) *bat_active;
	usRegHoldingBuf[4] = (int16_t) *bat_chrgng;
}

void mode_settings_init(void)
{
	/* ---------- Set status flags for the battery management ---------- */
	*bat_active = STAT_ACT_B0;				// Bat 3 is active on default
	*bat_chrgng = STAT_CHRG_NONE;			// No battery charging
	
	/* --- Set the holding registers for settings --- */
	*MANUAL_MODE	   = false;				// usRegHoldingBuf[0] = false;				// MANUAL_MODE
	usRegHoldingBuf[1] = NUM_2_BAT;			// NUM_BATs
	usRegHoldingBuf[2] = BAT_CELLS;			// BAT_CELLS
	usRegHoldingBuf[3] = STAT_ACT_B0;		// ACTIVE_BAT
	usRegHoldingBuf[4] = STAT_CHRG_NONE;	// CHRGNG_BAT
	*WIRELESS_MODE	   = false;					// usRegHoldingBuf[5] = false;				// COMM_MODE
	*NEW_SETTINGS	   = false;					// usRegHoldingBuf[6] = false;				// NEW_SETTINGS
	*CHRG_CYCLE		   = false;					// usRegHoldingBuf[7] = false;				// CHRG_CYCLE active?		
	*EMERGENCY_STOP	   = false;				// usRegHoldingBuf[8] = false;				// EMERGENCY_STOP active?
}

/*
 * Initializes timer registers (TIMER 0 8-Bit). 
 */
void timer_init(void){
	TIMSK = (1 << TOIE0);
	// Prescaler of 1024: 	t_interval = ( 2^8 * 1024 ) / 7372800 = 0.036s
	TCCR0 = ( (1 << CS01) | (1 << CS01) | (1 << CS00) );
	TCNT0 = 0;
	adc_timer_ovf_cnt = 0;
	wimod_timer_ovf_cnt = 0;
}

/*
 * Initializes output pins used in the management routines. 
 */
void ctrl_pin_init(void) {
	// Set pins PA0...PA7 as OUTPUT in GPIO Register A
	DDRA |=  ( (1 << PA7) | (1 << PA6) | (1 << PA5) | (1 << PA4)  | (1 << PA3) | (1 << PA2) | (1 << PA1) | (1 << PA0) );
	// Set all pins to zero in PORTA
	PORTA &= ~ ( (1 << PA7) | (1 << PA6) | (1 << PA5) | (1 << PA4)  | (1 << PA3) | (1 << PA2) | (1 << PA1) | (1 << PA0) );
}


/*
 * Configure the LoRa wireless module. 
 * 
 * Only settings that are changed are the Group Addr. and Device Addr.
 */
void config_lora_module(void){
	TWiMOD_HCI_Message configMsg;
	configMsg.SapID = DEVMGMT_ID;								// 0x01
	configMsg.MsgID = DEVMGMT_MSG_SET_RADIO_CONFIG_REQ;			// 0x11
	
	/* --------------- Payload -------------- */
	configMsg.Payload[0] = 0x00;		// Store NVM Flag
	/* ---------- Radio Configuration Field ---------- */
	configMsg.Payload[1] = 0x00;						// Radio Mode
	configMsg.Payload[2] = 0x25;						// Group Address
	configMsg.Payload[3] = 0x25;						// Tx Group Address
	configMsg.Payload[4] = 0x11;						// Device Address [low-byte]
	configMsg.Payload[5] = 0x47;						// Device Address [high-byte]
	configMsg.Payload[6] = 0x11;						// Tx Device Address [low-byte]
	configMsg.Payload[7] = 0x47;						// Tx Device Address [high-byte]
	configMsg.Payload[8] = 0x00;						// Modulation: 0x00 == LoRa
	configMsg.Payload[9] = 0x99;						// RF Carrier Frequency [least significant bits]
	configMsg.Payload[10] = 0x61;						// RF Carrier Frequency [intermediate bits]
	configMsg.Payload[11] = 0xd9;						// RF Carrier Frequency [most significant bits]
	configMsg.Payload[12] = 0x00;						// LoRa Signal Bandwidth
	configMsg.Payload[13] = 0x0b;						// LoRa Spreading Factor
	configMsg.Payload[14] = 0x02;						// Error Coding
	configMsg.Payload[15] = 0x11;						// Power level
	configMsg.Payload[16] = 0x00;						// Tx control
	configMsg.Payload[17] = 0x01;						// Rx control
	configMsg.Payload[18] = 0xb8;						// Rx window time [low byte]
	configMsg.Payload[19] = 0x0b;						// Rx window time [high byte]
	configMsg.Payload[20] = 0x07;						// LED control
	configMsg.Payload[21] = 0x03;						// Misc. Options
	configMsg.Payload[22] = 0x02;						// FSK Datarate
	configMsg.Payload[23] = 0x00;						// Automatic Power Saving
	configMsg.Payload[24] = 0x00;						// LBT Threshold [low-byte]
	configMsg.Payload[25] = 0x00;						// LBT Threshold [high-byte]
	/* ------------ Length ------------ */
	configMsg.Length = 1 + 25;

	WiMOD_HCI_SendMessage(&configMsg);
	
	/*memset(&configMsg, 0, sizeof(TWiMOD_HCI_Message));
	configMsg.SapID = 0x01;			// DEVMGMT_ID
	configMsg.MsgID = 0x13;			// DEVMGMT_MSG_GET_RADIO_CONFIG_REQ
	configMsg.Length = 0;
	WiMOD_HCI_SendMessage(&configMsg);*/
}
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

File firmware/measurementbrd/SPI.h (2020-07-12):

/*
 * SPI.h
 *
 * Created: 11.11.2019 12:42:03
 *  Author: patrickl
 */ 


#ifndef SPI_H_
#define SPI_H_
#include <avr/io.h>

/************************************************************************/
/* Mapping SPI pins ADC MCP33131-05 onto pins ATmega64                  */
/* ATmega64         ADC													*/
/* --------		   ------											*/
/* PB0 (~SS0)      CNVST0												*/
/* PB1 (SCK)        SCLK												*/
/* PB2 (MOSI)		none												*/
/* PB3 (MISO)     SDO_{0..3}											*/
/* PC7 (~SS1)      CNVST1												*/
/*   ...												*/
/* PC1 (~SS7)      CNVST7												*/
/************************************************************************/


/* Slave select lines for the external ADCs */

#define DD_SCK		PB1
#define DD_MOSI		PB2
#define DD_MISO		PB3
#define DD_SS0		PB0		// V_BAT_0+

#define DD_SS1		PC7		// V_BAT_1+
#define DD_SS2		PC6		// V_BAT_2+
#define DD_SS3		PC5		// V_BAT_3+
#define DD_SS4		PC4		// V_SOLAR+
#define DD_SS5		PC3		// I_SOLAR
#define DD_SS6		PC2		// I_CHARGE
#define DD_SS7		PC1		// I_LOAD



void spi_init();
void spi_tx(uint8_t slave);



#endif /* SPI_H_ */

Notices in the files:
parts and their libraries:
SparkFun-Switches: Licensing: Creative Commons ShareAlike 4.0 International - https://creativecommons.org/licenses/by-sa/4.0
